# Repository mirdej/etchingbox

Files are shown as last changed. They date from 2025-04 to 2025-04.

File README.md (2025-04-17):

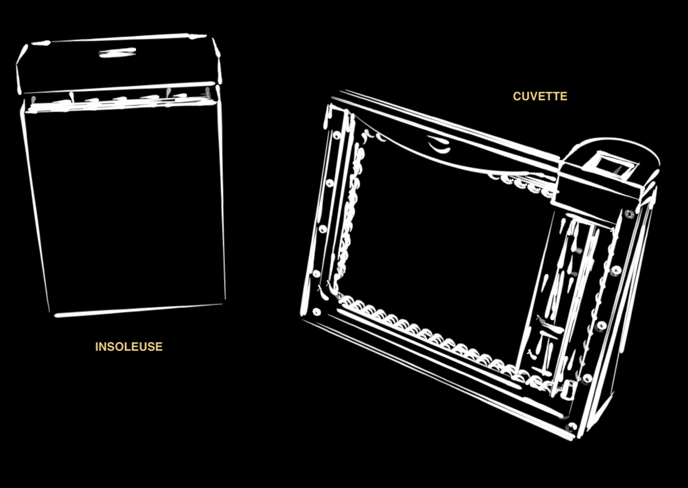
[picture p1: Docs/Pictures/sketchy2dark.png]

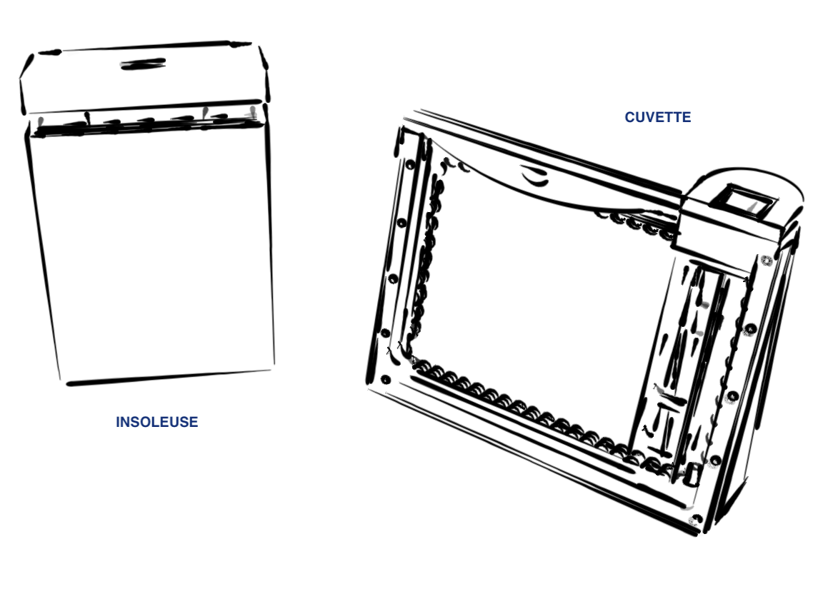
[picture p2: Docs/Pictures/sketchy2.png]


# AETZBOX
### DIY Mobile PCB Etching KIT

## The Idea 
Build a portable / mobile PCB etching workstation that fulfills these criteria
* waterproof
* able to etch 100x160mm double sided boards with 8mil precision
* low cost.  total bill of materials should not exceed 150 CHF
* diy approach, mostly laser cut plexi and easily sourceable materials
* fits in a RAKO Box

Some guiding ideas
* use very little but always fresh chemicals 
* good heat management: etching has to be done at 45-50 degrees celsius, developer has to be kept at >20 degrees as well (in my workshop, temperatures can easily drop below 16 degrees and developing is a pain).
* all material and chemicals travel in the box. liquid waste can travel in the box as well until it can properly disposed of.
* should be easy to clean. no electronics exposed to moisture. 
* as few as possible switches and electrical contacts exposed to the harsh etching environment
* self illuminating

## More Info
https://wiki.sgmk-ssam.ch/index.php/EtchingBox

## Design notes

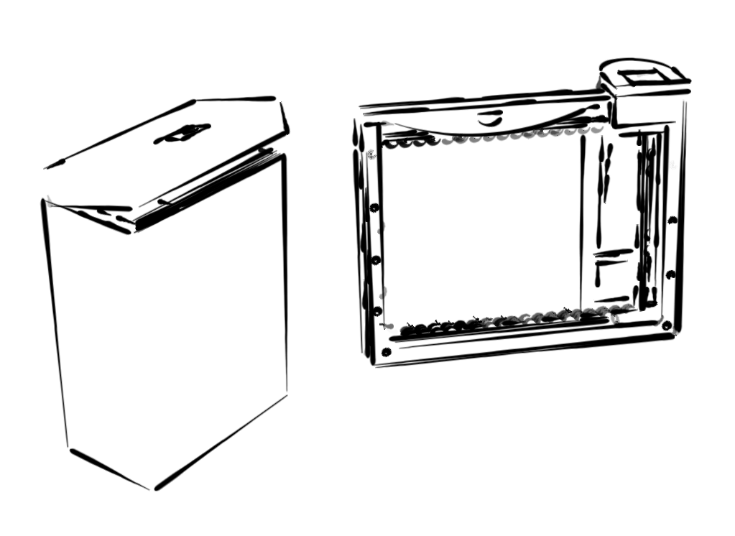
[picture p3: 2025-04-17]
Docs/Pictures/sketchy.png

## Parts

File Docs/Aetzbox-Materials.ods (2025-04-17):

Category | Description | Value | Qty | Price | Link
Total Cost |  |  |  | CHF 101.04
Chemicals
 | Developer | NaOH | 10g | CHF 0.13 | https://www.reichelt.com/ch/de/shop/produkt/entwickler_natriumhydroxid_1_kg-396207
 | Etchant | Natriumpersulfat | 600g | CHF 8.00 | https://www.reichelt.com/ch/de/shop/produkt/_etzmittel_natriumpersulfat_600_g_-23424
 | Presentisized PCB Material | Bungard 160x100mm one sided |  | CHF 2.15 | https://www.reichelt.com/ch/de/shop/produkt/fotoplatine_einseitig_160x100mm_1_5mm_35_-33767
 |  | Bungard 160x100mm double sided |  | CHF 2.70 | https://www.reichelt.com/ch/de/shop/produkt/fotoplatine_zweiseitig_160x100mm_1_5mm_35_-33774
Construction Material
 | PLA | Extrudr NX2 Black | About 850 grams, Total print time about 20 hours | CHF 25.50 | https://www.3dware.ch/en/search/93a7e009-72cb-4a7e-b261-3c64b5b91971?Query=01122210.25
 | Silicone | TFC Baseline 200 | About 300 grams | CHF 6.60 | https://trollfactory.de/Anwendungen/Modellbau/TFBL20010/TFC-Baseline-200-Silikon-Abformsilikon-Shore-35-1-1-transluzent-Groesse-10kg-5kg-5kg
 | Acrylic | 5mm clear, 5mm white opal, 3mm clear | About 50x50cm | CHF 25.00 | https://www.jumbo.ch/de/bauen-renovieren/bedachungsmaterialien/doppelstegplatten/acrylglas--50--50--05-cm/p/7009657
 | Screws | M4x40, Inox A2 | 14 | CHF 4.20 | https://www.bossard.com/eshop/ch-en/screws-and-bolts-with-internal-drive/hexalobular-6-lobe-socket-countersunk-flat-head-screws-fully-threaded/p/3803/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
 | Nuts | M4, Inox A2 | 14 | CHF 0.84 | https://www.bossard.com/eshop/ch-en/products/fastening-technology/standard-fastening-elements/nuts/hex-nuts/hex-nuts-08d/p/628/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
 | Screws | K22x6 |  | CHF 0.50 | https://www.bossard.com/eshop/ch-en/fastening-technology/direct-assembly-screws/direct-assembly-screws-for-plastics/ejot-pt/p/11308/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
Electronics
 | Temperature Sensor | Stainless Steel Waterproof DS18b20 | 1 | CHF 0.80 | https://www.aliexpress.com/item/32676135779.html
 | Aquarium Pump | TZT DC6-12V R385 Aquarium Fish Tank Round Water Air DC Diaphragm Pump | 1 | CHF 3.00 | https://www.aliexpress.com/item/1005003293750070.html
 | Heater | 304 Stainless Steel Cartridge Heater 8x80mm 60W 12V | 1 | CHF 2.00 | https://www.aliexpress.com/item/32906278667.html
 | Display | 0.96 inch oled IIC Serial White OLED Display Module 128X64 I2C SSD1315 12864 LCD | 2 | CHF 2.00 | https://www.aliexpress.com/item/4001028369082.html
 | ESP32 | ESP32-S3-WROOM | 2 | CHF 10.00 | https://www.digikey.ch/en/products/detail/espressif-systems/ESP32-S3-WROOM-1-N16/16162647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
 | PCBs | JLCPCB |  | CHF 5.00
 | DC-DC Converter | 919-R-78K3.3-0.5 | 2 | CHF 5.60 | https://eu.mouser.com/ProductDetail/RECOM-Power/R-78K3.3-0.5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
 | UV-Leds | S2-2835UVTA-0.2W |  |  | https://jlcpcb.com/partdetail/Tuozhan-S2_2835UVTA_02W/C2827317
 | Assembled UV-Board | JLCPCBA | 2 | CHF 10.00

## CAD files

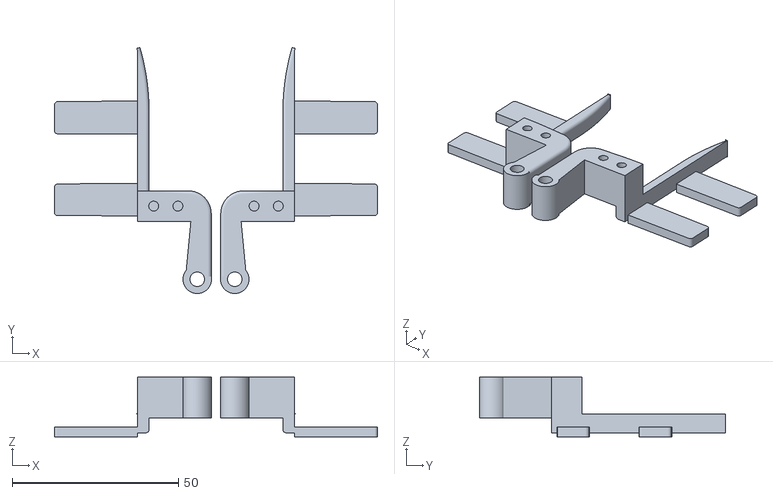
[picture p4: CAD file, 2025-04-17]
3D/STL/Insoleuse-Lid-Hinge.stl
97.3 x 74.1 x 18.0

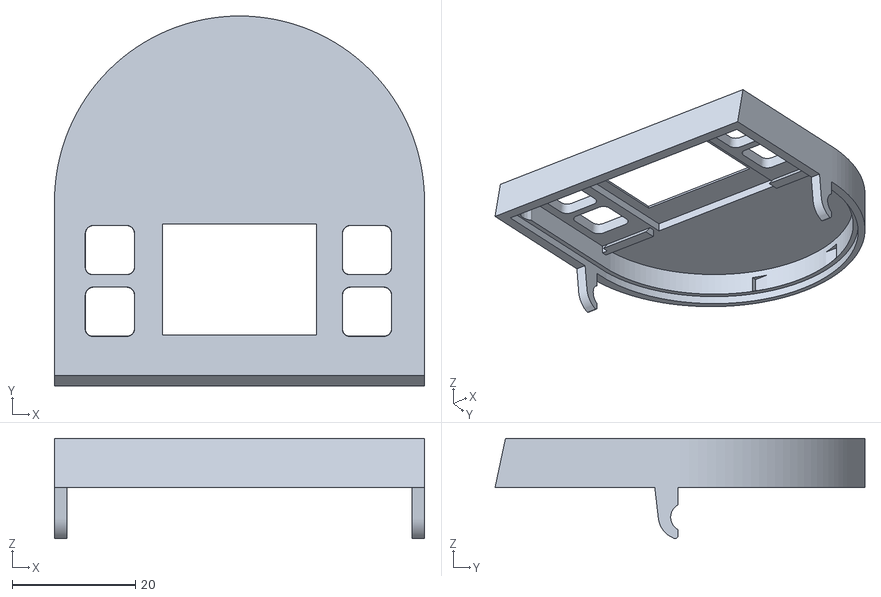
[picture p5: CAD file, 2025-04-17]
3D/STL/Cuvette-TopCover.stl
60.0 x 60.0 x 16.3

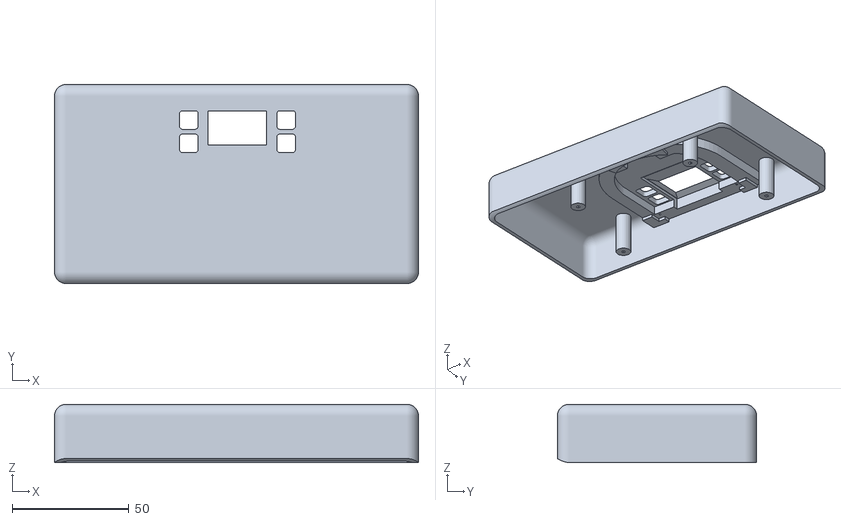
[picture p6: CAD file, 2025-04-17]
3D/STL/Insoleuse-Lid.stl
155.8 x 85.2 x 25.0

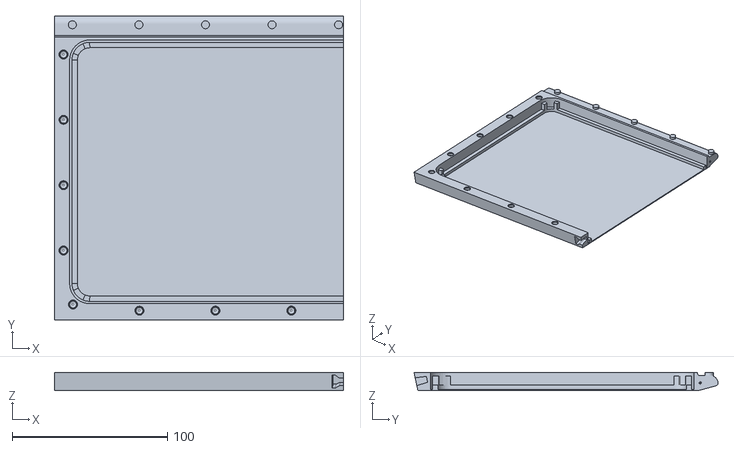
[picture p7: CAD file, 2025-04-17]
3D/STL/Cuvette-Back.stl
186.4 x 196.0 x 11.9

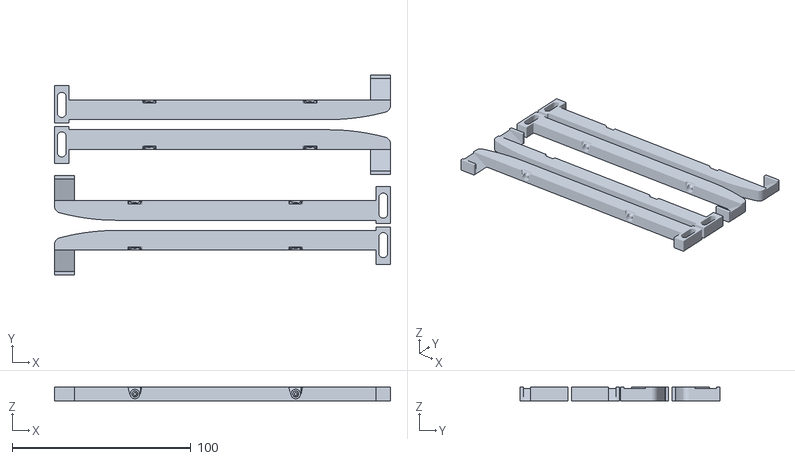
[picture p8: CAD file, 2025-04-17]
3D/STL/Insoleuse-Guides.stl
188.0 x 112.0 x 8.00

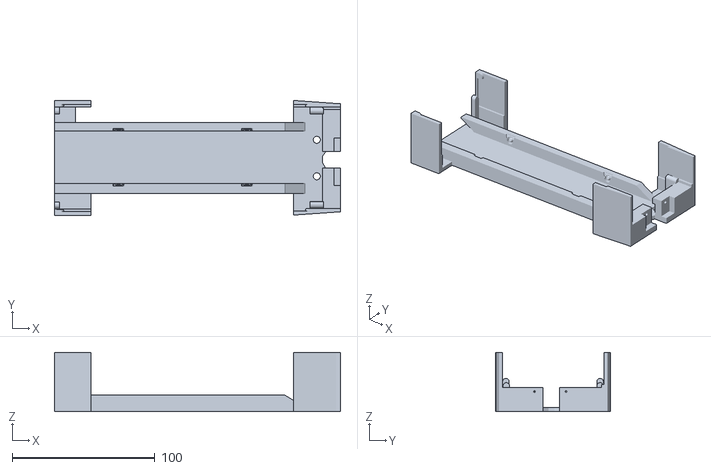
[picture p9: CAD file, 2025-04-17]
3D/STL/Insoleuse_GuideAndPCB-Holder.stl
200.6 x 80.9 x 41.6

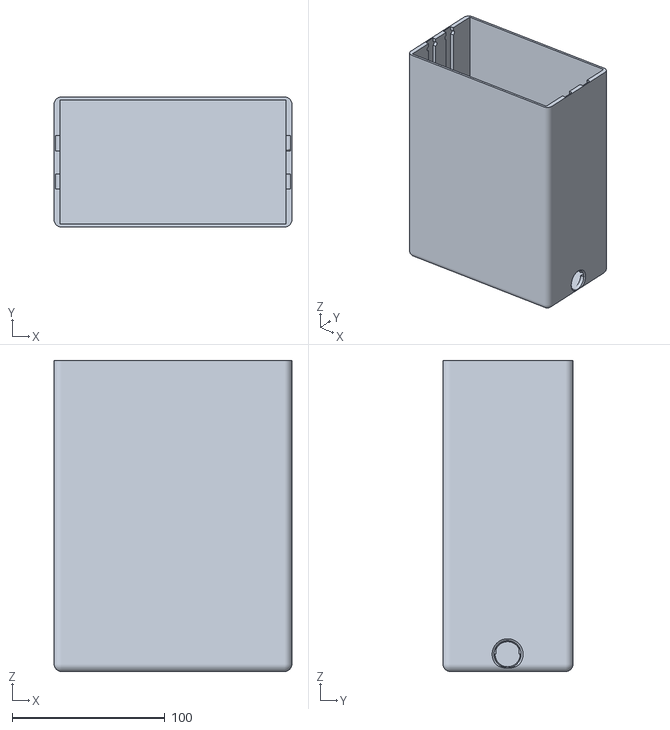
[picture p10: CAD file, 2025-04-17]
3D/STL/Insoleuse-Box.stl
155.8 x 85.2 x 203.6

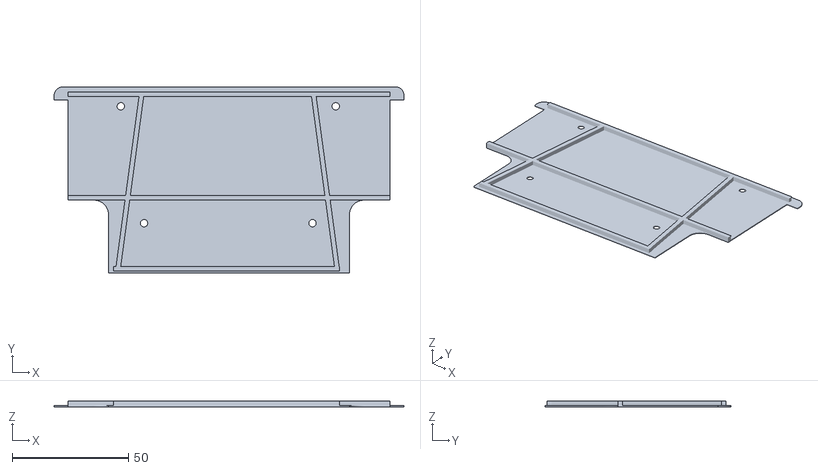
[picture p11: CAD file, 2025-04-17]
3D/STL/Insoleuse-Lid-Cover.stl
150.6 x 80.2 x 2.60

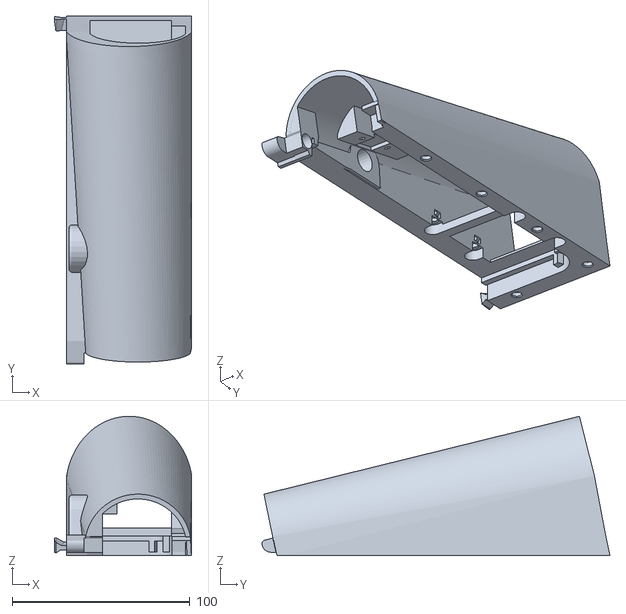
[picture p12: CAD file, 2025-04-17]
3D/STL/Cuvette-BackPumpCover.stl
77.4 x 196.0 x 78.5

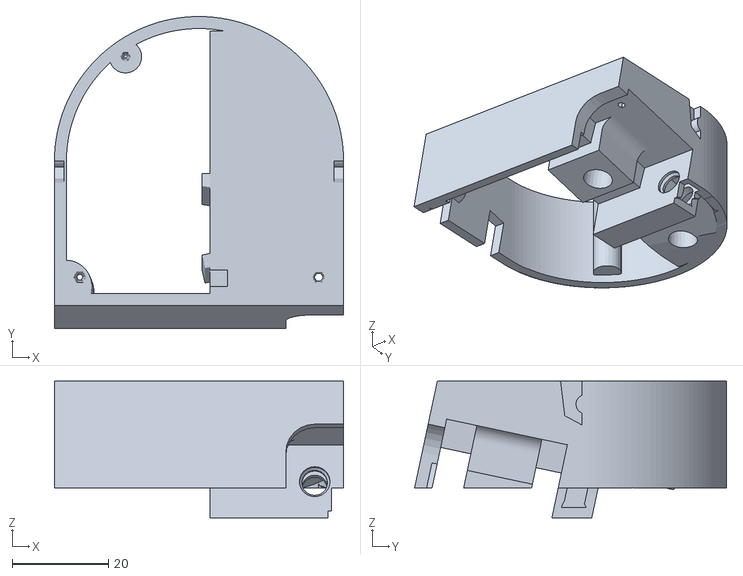
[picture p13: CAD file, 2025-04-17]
3D/STL/Cuvette-Top.stl
60.0 x 64.7 x 28.4

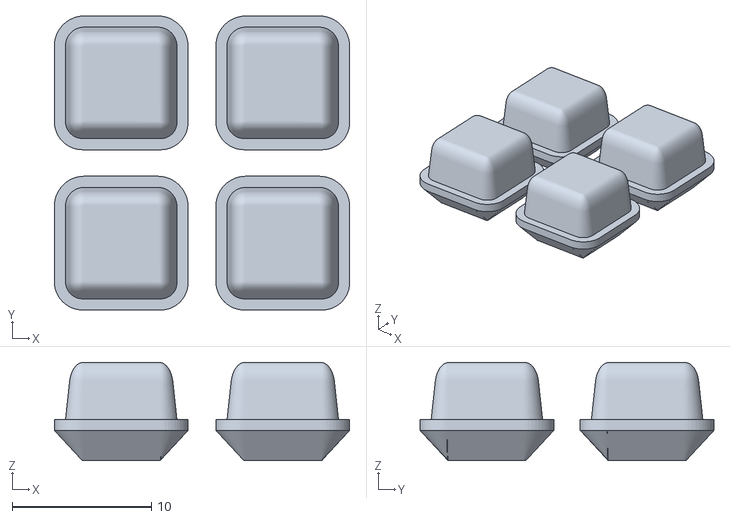
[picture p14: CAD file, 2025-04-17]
3D/STL/Insoleuse-Boutons.stl
21.2 x 21.1 x 7.04

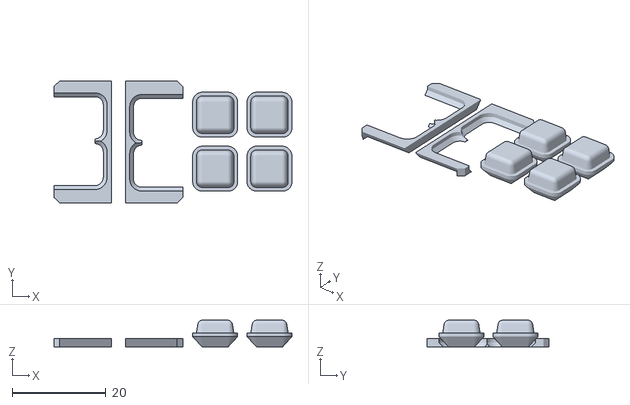
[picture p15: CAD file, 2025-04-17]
3D/STL/Cuvette-Boutons.stl
50.8 x 26.0 x 5.68

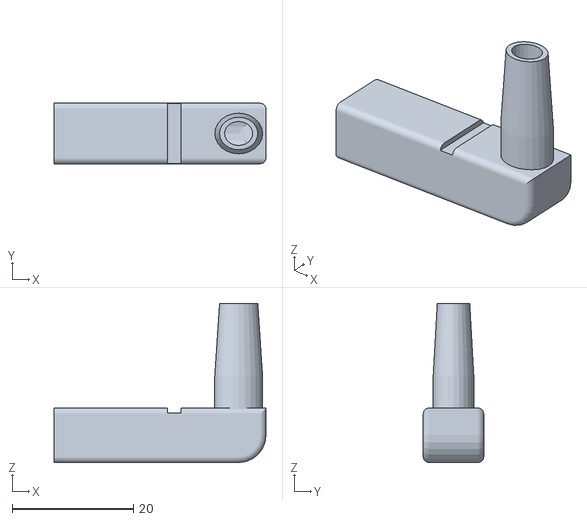
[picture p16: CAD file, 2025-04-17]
3D/STL/Cuvette-Blasfuss.stl
35.0 x 10.0 x 26.3

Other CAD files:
3D/Cuvette-Assembled.skp
3D/Cuvette-Mold-Bouchon.skp
3D/Cuvette-Mold-Cuvette.skp
3D/Cuvette-Mold-Lid.skp
3D/Cuvette-Mold-TopCover.skp
3D/Cuvette-Parts.skp
3D/Insoleuse-Assembled.skp
3D/Insoleuse-Parts.skp

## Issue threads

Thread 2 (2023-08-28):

heating chamber

5shekel, 2023-08-28:
hey, i love the etchingbox. had the pleasure of interacting with it at the cccamp.

i am missing a few things, mostly BOM of the heating chamber.
tips on the airflow/pump and heating element (ab)used will help.

https://github.com/mirdej/etchingbox/assets/222526/f30ac814-8d48-4f98-9d1f-8d26fef8e23c

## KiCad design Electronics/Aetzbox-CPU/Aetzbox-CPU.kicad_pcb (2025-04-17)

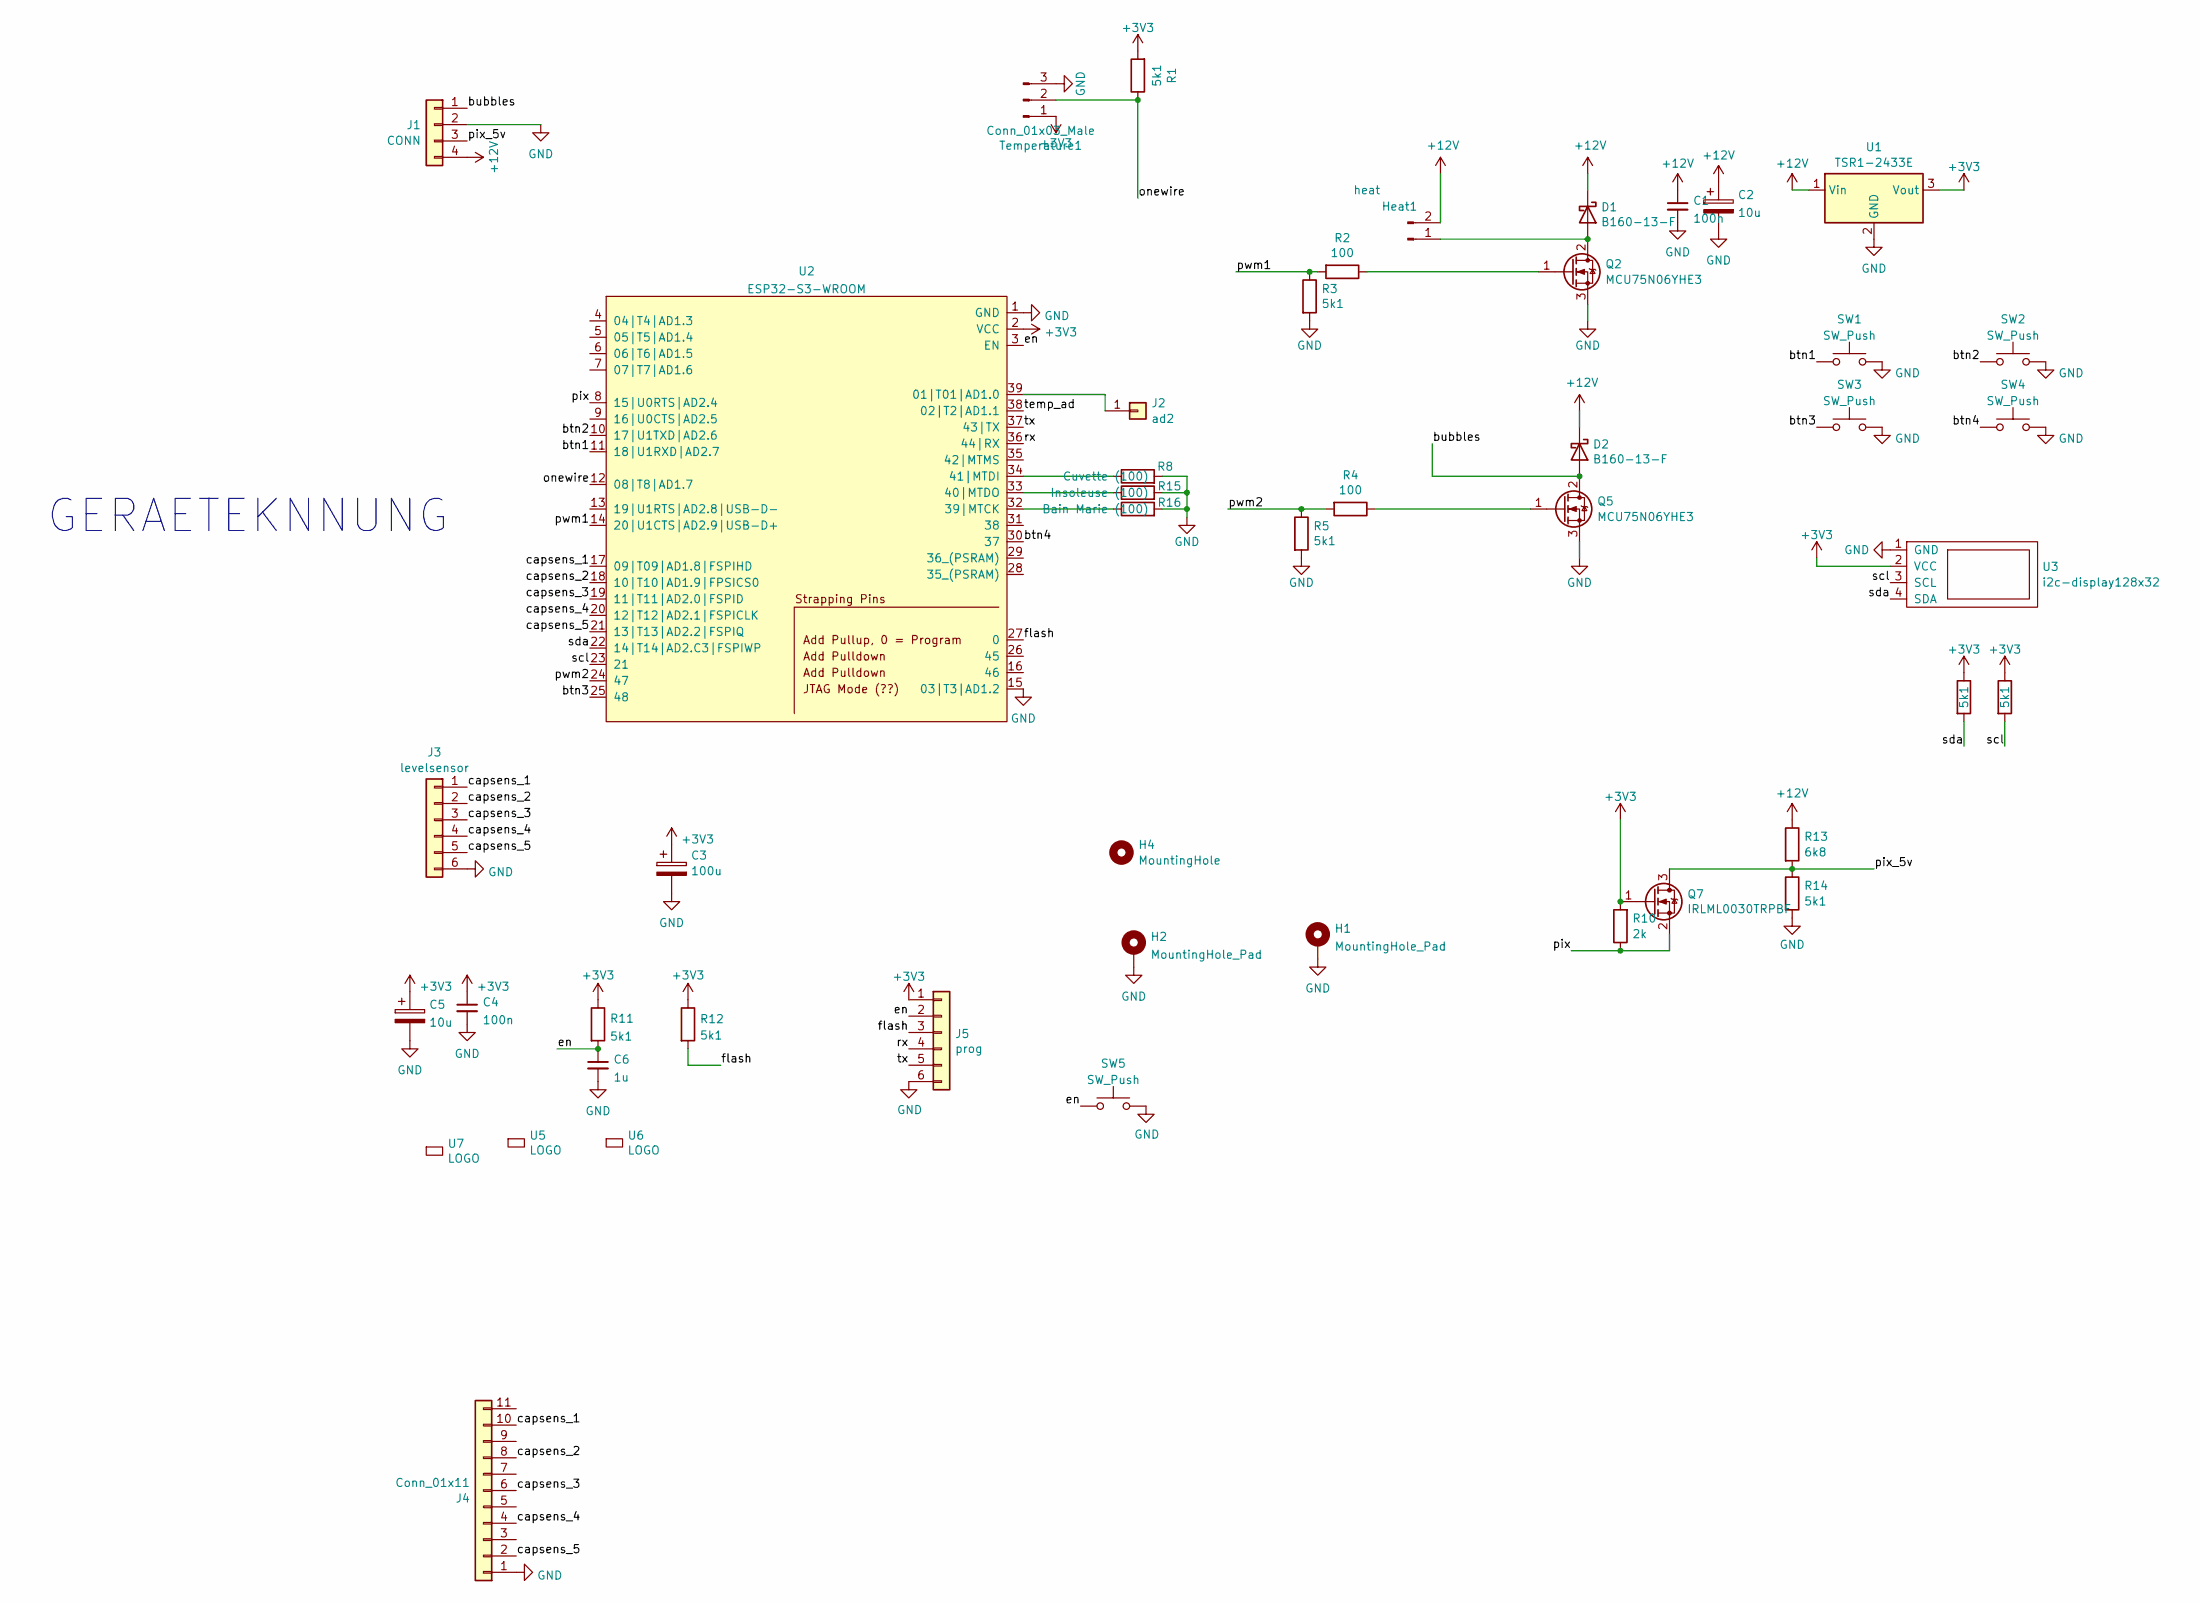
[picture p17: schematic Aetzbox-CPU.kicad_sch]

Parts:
C1, C4: 100n; C_0603_1608Metric_Pad1.05x0.95mm_HandSolder
C2, C5: 10u; C_1206_3216Metric_Pad1.42x1.75mm_HandSolder
C3: 100u; CP_EIA-6032-20_AVX-F
C6: 1u; C_0603_1608Metric_Pad1.05x0.95mm_HandSolder
D1, D2: B160-13-F; D_SMA-SMB_Universal_Handsoldering
H1, H2: MountingHole_Pad; MountingHole_2.5mm_Pad
H4: MountingHole; MountingHole_2.5mm
Heat1: heat; Molex_Mini-Fit_Jr_5566-02A_2x01_P4.20mm_Vertical
J1: CONN; Molex_Mini-Fit_Jr_5569-04A2_2x02_P4.20mm_H+V
J2: ad2; Solderpad_1mm
J3: levelsensor; PinSocket_1x06_P1.27mm_Vertical
J4: Conn_01x11; Molex_200528-0100_1x10-1MP_P1.00mm_Horizontal
J5: prog; ESP-POGO-PROG-THT
Q2, Q5: MCU75N06YHE3; TO-252-2
Q7: IRLML0030TRPBF; SOT-23
R1, R3, R5, R6, R7, R11, R12, R14: 5k1; R_0805_2012Metric
R2, R4: 100; R_0805_2012Metric
R8: Cuvette (100); R_0805_2012Metric
R10: 2k; R_0805_2012Metric
R13: 6k8; R_0805_2012Metric
R15: Insoleuse (100); R_0805_2012Metric
R16: Bain Marie (100); R_0805_2012Metric
SW1, SW2, SW3, SW4: SW_Push; Alps_Tactile_Switch
SW5: SW_Push; MiniButtonPLCC4
Temperature1: Conn_01x03_Male; Molex_KK-254_AE-6410-03A_1x03_P2.54mm_Vertical
U1: TSR1-2433E; Converter_DCDC_TRACO_TSR1-xxxxE_THT
U2: ESP32-S3-WROOM
U3: i2c-display128x32; Bangood_I2C_Display
U5: LOGO; logo_anyma_tiny
U6: LOGO; logo_sgmk
U7: LOGO; OSHW-Logo2_7.3x6mm_SilkScreen

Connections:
+3V3: C3.1, C4.1, C5.1, J5.1, Q7.1 (G), R1.2, R6.1, R7.1, R10.2, R11.1, R12.1, Temperature1.1, U1.3 (Vout), U2.2 (VCC), U3.2 (VCC)
+12V: C1.1, C2.1, D1.1 (K), D2.1 (K), Heat1.2, J1.4, R13.1, U1.1 (Vin)
/btn1: SW1.1, U2.11 (18|U1RXD|AD2.7)
/btn2: SW2.1, U2.10 (17|U1TXD|AD2.6)
/btn3: SW3.1, U2.25 (48)
/btn4: SW4.1, U2.30 (37)
/bubbles: D2.2 (A), J1.1, Q5.2 (D)
/capsens_1: J3.1, J4.10, U2.17 (09|T09|AD1.8|FSPIHD)
/capsens_2: J3.2, J4.8, U2.18 (10|T10|AD1.9|FPSICS0)
/capsens_3: J3.3, J4.6, U2.19 (11|T11|AD2.0|FSPID)
/capsens_4: J3.4, J4.4, U2.20 (12|T12|AD2.1|FSPICLK)
/capsens_5: J3.5, J4.2, U2.21 (13|T13|AD2.2|FSPIQ)
/en: C6.1, J5.2, R11.2, SW5.2, U2.3 (EN)
/flash: J5.3, R12.2, U2.27 (0)
/onewire: R1.1, Temperature1.2, U2.12 (08|T8|AD1.7)
/pix: Q7.2 (S), R10.1, U2.8 (15|U0RTS|AD2.4)
/pix_5v: J1.3, Q7.3 (D), R13.2, R14.1
/pwm1: R2.2, R3.1, U2.14 (20|U1CTS|AD2.9|USB-D+)
/pwm2: R4.2, R5.1, U2.24 (47)
/rx: J5.4, U2.36 (44|RX)
/scl: R7.2, U2.23 (21), U3.3 (SCL)
/sda: R6.2, U2.22 (14|T14|AD2.C3|FSPIWP), U3.4 (SDA)
/temp_ad: U2.38 (02|T2|AD1.1)
/tx: J5.5, U2.37 (43|TX)
GND: C1.2, C2.2, C3.2, C4.2, C5.2, C6.2, H1.1, H2.1, J1.2, J3.6, J4.1, J5.6, Q2.3 (S), Q5.3 (S), R3.2, R5.2, R8.2, R14.2, R15.2, R16.2, SW1.2, SW2.2, SW3.2, SW4.2, SW5.1, Temperature1.3, U1.2 (GND), U2.1 (GND), U2.15 (03|T3|AD1.2), U2.40 (GND), U2.41 (GND), U3.1 (GND)
unnamed: D1.2 (A), Heat1.1, Q2.2 (D)
unnamed: J2.1, U2.39 (01|T01|AD1.0)
unnamed: Q2.1 (G), R2.1
unnamed: Q5.1 (G), R4.1
unnamed: R16.1, U2.32 (39|MTCK)
unnamed: R15.1, U2.33 (40|MTDO)
unnamed: R8.1, U2.34 (41|MTDI)

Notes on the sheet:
GERAETEKNNUNG

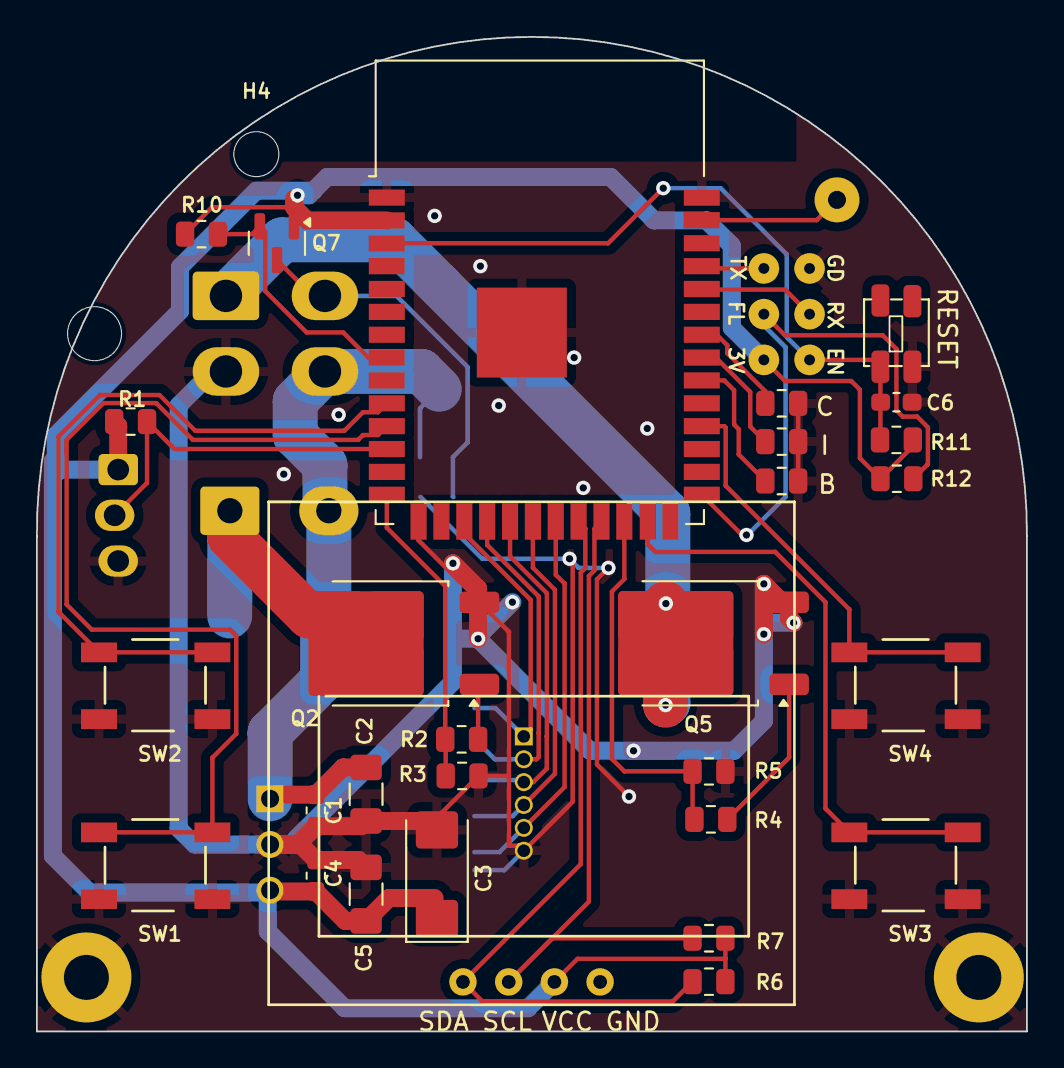
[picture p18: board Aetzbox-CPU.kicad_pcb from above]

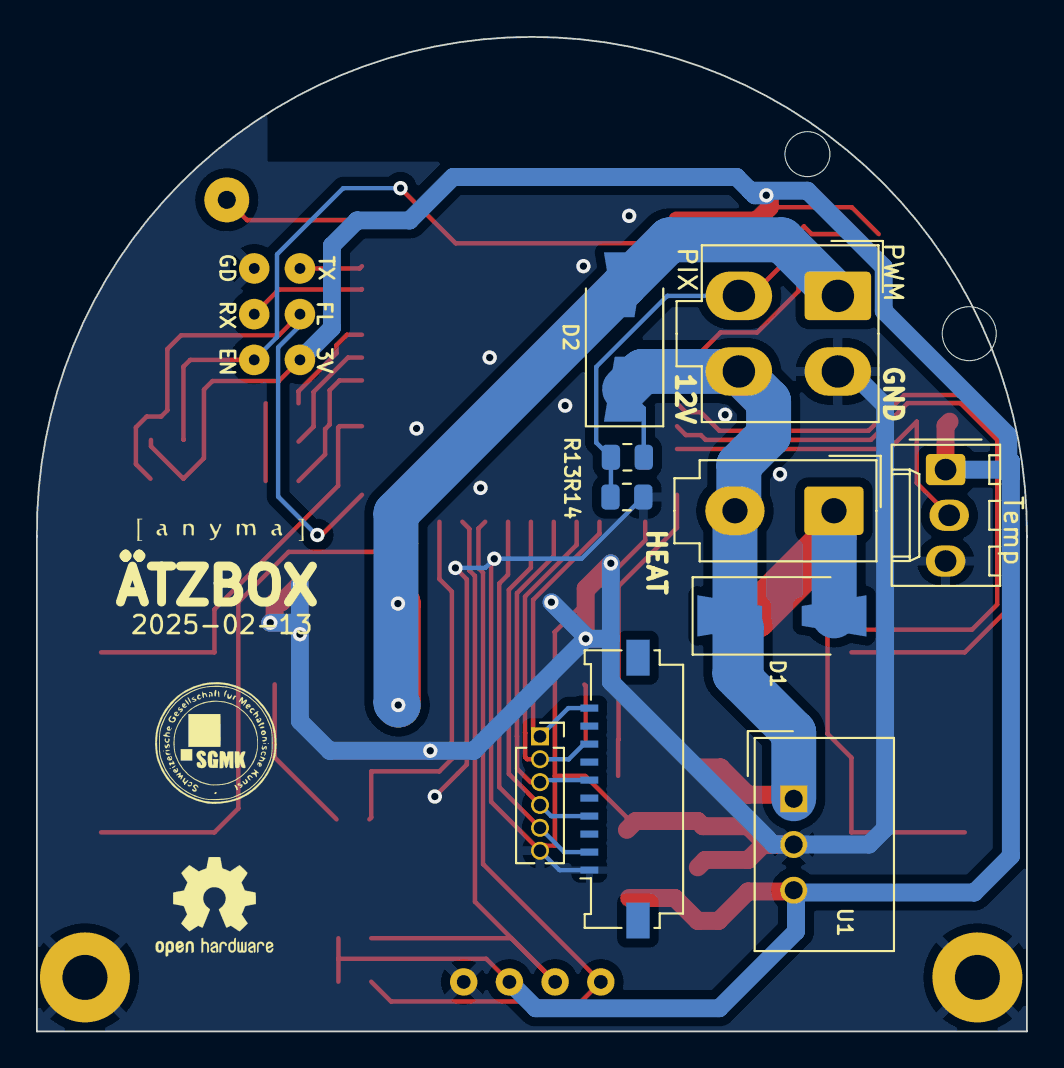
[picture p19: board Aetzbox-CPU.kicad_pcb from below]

Board: 2 copper layers, 55.0 x 55.3 mm, 47 parts (14 on the bottom side), 31 nets.

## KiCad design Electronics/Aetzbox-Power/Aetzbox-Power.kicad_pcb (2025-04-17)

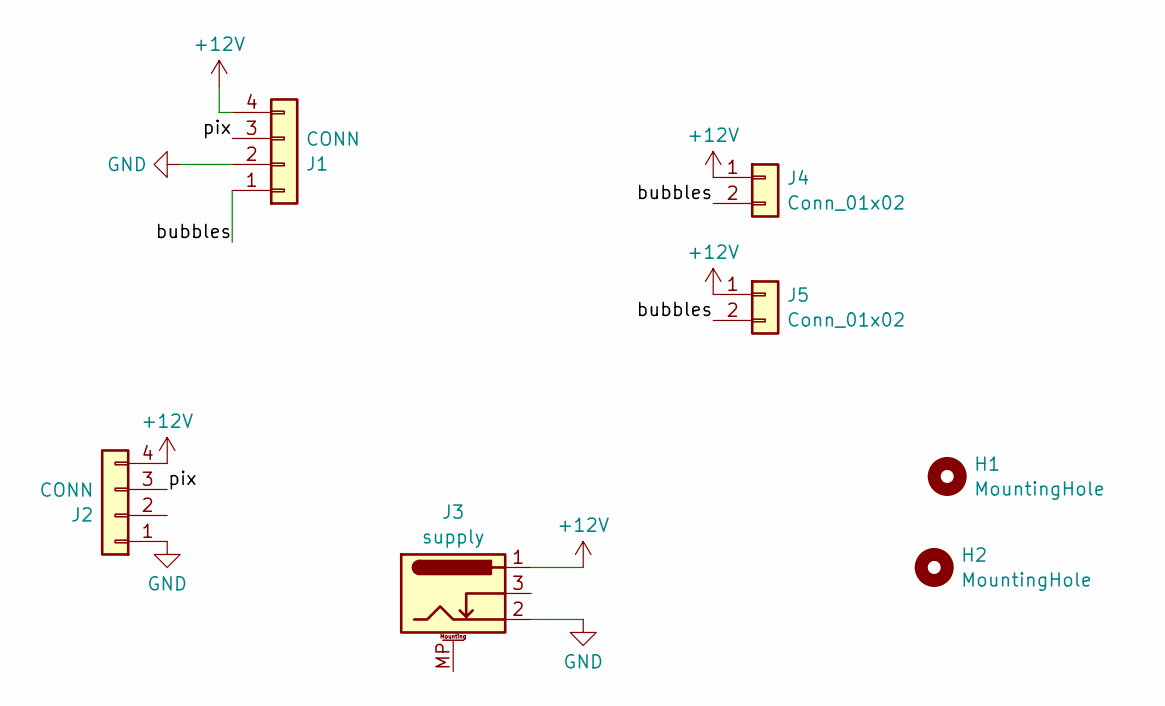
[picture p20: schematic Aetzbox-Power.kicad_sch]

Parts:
H1, H2: MountingHole; MountingHole_3.2mm_M3_DIN965
J1: CONN; Molex_Mini-Fit_Jr_5569-04A2_2x02_P4.20mm_H+V
J2: CONN; PinHeader_1x04_P2.54mm_Horizontal
J3: supply; BarrelJack_CUI_PJ-079BH_Horizontal
J4, J5: Conn_01x02; PinHeader_1x02_P2.54mm_Horizontal

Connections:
+12V: J1.4, J2.4, J3.1, J4.1, J5.1
/bubbles: J1.1, J4.2, J5.2
/pix: J1.3, J2.3
GND: J1.2, J2.1, J3.2

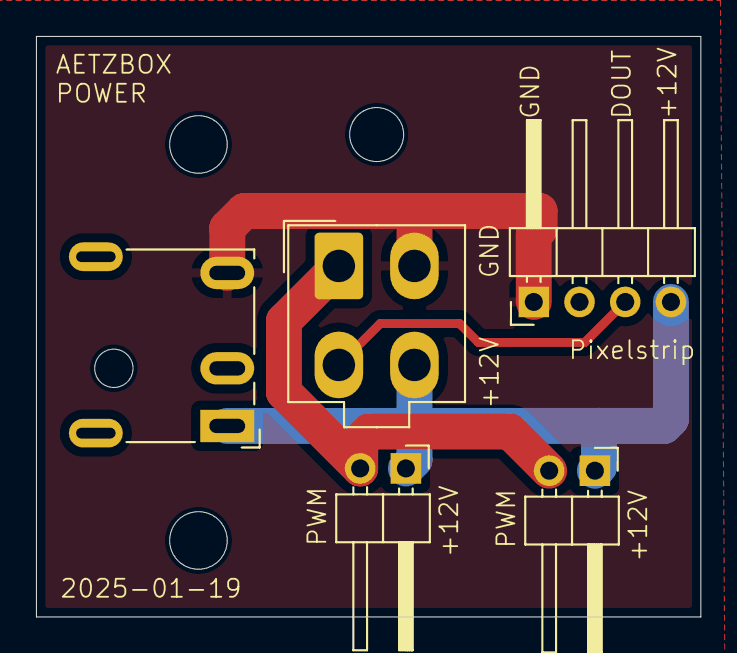
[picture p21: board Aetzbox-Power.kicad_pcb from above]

Board: 2 copper layers, 36.9 x 32.2 mm, 7 parts (0 on the bottom side), 4 nets.

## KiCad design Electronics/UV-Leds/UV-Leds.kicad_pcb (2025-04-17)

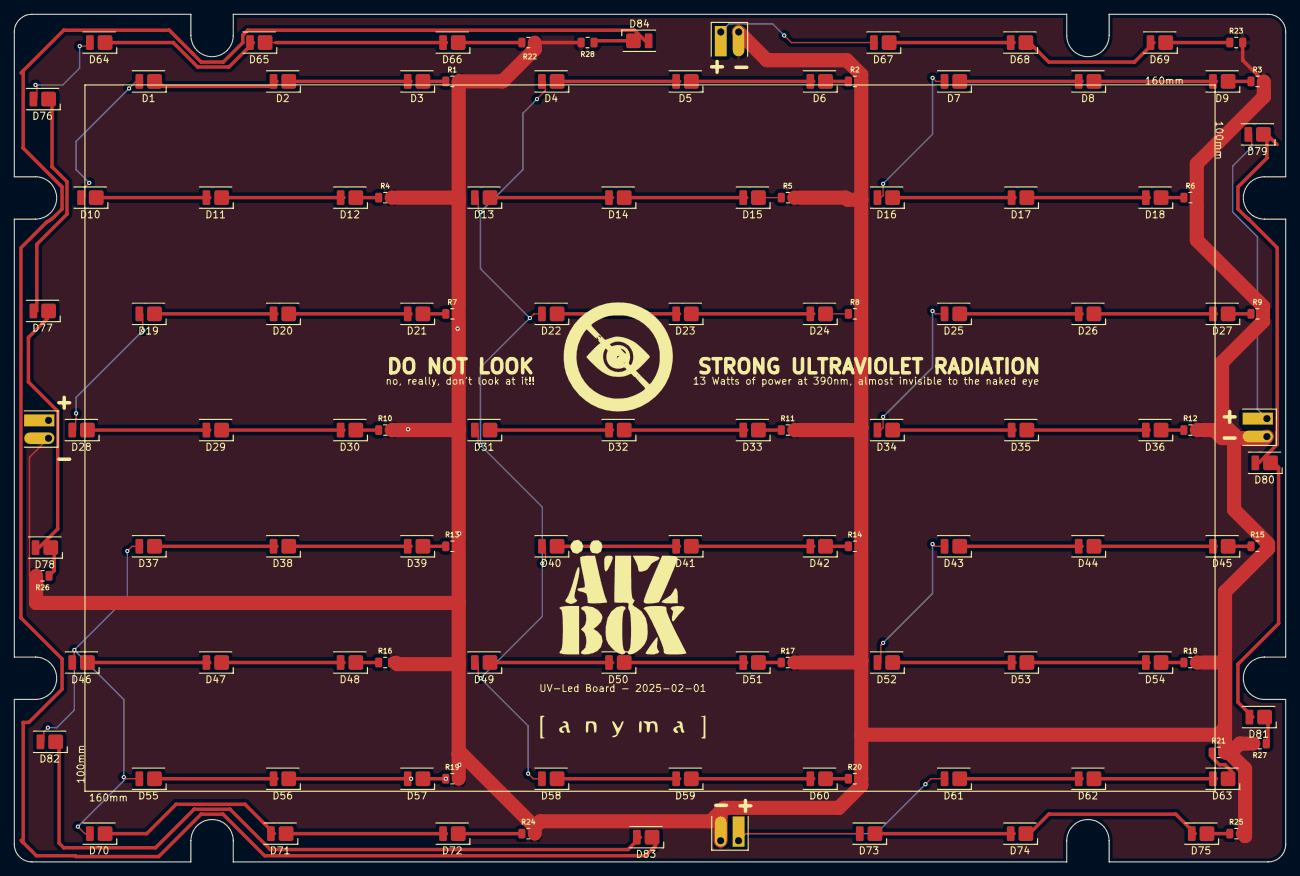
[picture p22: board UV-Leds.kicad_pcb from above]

Board: 2 copper layers, 180.0 x 120.0 mm, 119 parts (0 on the bottom side), 86 nets.

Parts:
D1, D2, D3, D4, D5, D6, D7, D8, D9, D10, D11, D12, D13, D14, D15, D16, D17, D18, D19, D20, D21, D22, D23, D24, D25, D26, D27, D28, D29, D30, D31, D32, D33, D34, D35, D36, D37, D38, D39, D40, D41, D42, D43, D44, D45, D46, D47, D48, D49, D50, D51, D52, D53, D54, D55, D56, D57, D58, D59, D60, D61, D62, D63, D64, D65, D66, D67, D68, D69, D70, D71, D72, D73, D74, D75, D76, D77, D78, D79, D80, D81, D82, D83, D84: LED; LED_2835_UV-S2-2835UVTA-0.2W
J1, J2, J3, J4: Conn_01x02; ComboPinhead_02
R1, R2, R3, R4, R5, R6, R7, R8, R9, R10, R11, R12, R13, R14, R15, R16, R17, R18, R19, R20, R21, R22, R23, R24, R25, R26, R27, R28: R; R_0805_2012Metric
U1: LOGO; logo_aetz_box
U2: LOGO; logo_dontt_look
U3: LOGO; logo_anyma

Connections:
+12V: D1.2 (A), D4.2 (A), D7.2 (A), D10.2 (A), D13.2 (A), D16.2 (A), D19.2 (A), D22.2 (A), D25.2 (A), D28.2 (A), D31.2 (A), D34.2 (A), D37.2 (A), D40.2 (A), D43.2 (A), D46.2 (A), D49.2 (A), D52.2 (A), D55.2 (A), D58.2 (A), D61.2 (A), D64.2 (A), D67.2 (A), D70.2 (A), D73.2 (A), D76.2 (A), D79.2 (A), D82.2 (A), J1.1, J2.1, J3.1, J4.1
GND: J1.2, J2.2, J3.2, J4.2, R1.2, R2.2, R3.2, R4.2, R5.2, R6.2, R7.2, R8.2, R9.2, R10.2, R11.2, R12.2, R13.2, R14.2, R15.2, R16.2, R17.2, R18.2, R19.2, R20.2, R21.2, R22.2, R23.2, R24.2, R25.2, R26.2, R27.2, R28.2
unnamed: D1.1 (K), D2.2 (A)
unnamed: D2.1 (K), D3.2 (A)
unnamed: D3.1 (K), R1.1
unnamed: D4.1 (K), D5.2 (A)
unnamed: D5.1 (K), D6.2 (A)
unnamed: D6.1 (K), R2.1
unnamed: D7.1 (K), D8.2 (A)
unnamed: D8.1 (K), D9.2 (A)
unnamed: D9.1 (K), R3.1
unnamed: D10.1 (K), D11.2 (A)
unnamed: D11.1 (K), D12.2 (A)
unnamed: D12.1 (K), R4.1
unnamed: D13.1 (K), D14.2 (A)
unnamed: D14.1 (K), D15.2 (A)
unnamed: D15.1 (K), R5.1
unnamed: D16.1 (K), D17.2 (A)
unnamed: D17.1 (K), D18.2 (A)
unnamed: D18.1 (K), R6.1
unnamed: D19.1 (K), D20.2 (A)
unnamed: D20.1 (K), D21.2 (A)
unnamed: D21.1 (K), R7.1
unnamed: D22.1 (K), D23.2 (A)
unnamed: D23.1 (K), D24.2 (A)
unnamed: D24.1 (K), R8.1
unnamed: D25.1 (K), D26.2 (A)
unnamed: D26.1 (K), D27.2 (A)
unnamed: D27.1 (K), R9.1
unnamed: D28.1 (K), D29.2 (A)
unnamed: D29.1 (K), D30.2 (A)
unnamed: D30.1 (K), R10.1
unnamed: D31.1 (K), D32.2 (A)
unnamed: D32.1 (K), D33.2 (A)
unnamed: D33.1 (K), R11.1
unnamed: D34.1 (K), D35.2 (A)
unnamed: D35.1 (K), D36.2 (A)
unnamed: D36.1 (K), R12.1
unnamed: D37.1 (K), D38.2 (A)
unnamed: D38.1 (K), D39.2 (A)
unnamed: D39.1 (K), R13.1
unnamed: D40.1 (K), D41.2 (A)
unnamed: D41.1 (K), D42.2 (A)
unnamed: D42.1 (K), R14.1
unnamed: D43.1 (K), D44.2 (A)
unnamed: D44.1 (K), D45.2 (A)
unnamed: D45.1 (K), R15.1
unnamed: D46.1 (K), D47.2 (A)
unnamed: D47.1 (K), D48.2 (A)
unnamed: D48.1 (K), R16.1
unnamed: D49.1 (K), D50.2 (A)
unnamed: D50.1 (K), D51.2 (A)
unnamed: D51.1 (K), R17.1
unnamed: D52.1 (K), D53.2 (A)
unnamed: D53.1 (K), D54.2 (A)
unnamed: D54.1 (K), R18.1
unnamed: D55.1 (K), D56.2 (A)
unnamed: D56.1 (K), D57.2 (A)
unnamed: D57.1 (K), R19.1
unnamed: D58.1 (K), D59.2 (A)
unnamed: D59.1 (K), D60.2 (A)
unnamed: D60.1 (K), R20.1
unnamed: D61.1 (K), D62.2 (A)
unnamed: D62.1 (K), D63.2 (A)
unnamed: D63.1 (K), R21.1
unnamed: D64.1 (K), D65.2 (A)
unnamed: D65.1 (K), D66.2 (A)
unnamed: D66.1 (K), R22.1
unnamed: D67.1 (K), D68.2 (A)
unnamed: D68.1 (K), D69.2 (A)
unnamed: D69.1 (K), R23.1
unnamed: D70.1 (K), D71.2 (A)
unnamed: D71.1 (K), D72.2 (A)
unnamed: D72.1 (K), R24.1
unnamed: D73.1 (K), D74.2 (A)
unnamed: D74.1 (K), D75.2 (A)
unnamed: D75.1 (K), R25.1
unnamed: D76.1 (K), D77.2 (A)
unnamed: D77.1 (K), D78.2 (A)
unnamed: D78.1 (K), R26.1
unnamed: D79.1 (K), D80.2 (A)
unnamed: D80.1 (K), D81.2 (A)
unnamed: D81.1 (K), R27.1
unnamed: D82.1 (K), D83.2 (A)
unnamed: D83.1 (K), D84.2 (A)
unnamed: D84.1 (K), R28.1

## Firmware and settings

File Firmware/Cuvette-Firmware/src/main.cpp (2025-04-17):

/*========================================================================================

[ a n y m a ]
AETZBOX
Cuvette

© 2024 Michael Egger AT anyma.ch

==========================================================================================*/
//                                                                                      LIB
#include <Arduino.h>
#include <FastLED.h>
#include <U8g2lib.h>
#include <OneWire.h>
#include <DallasTemperature.h>
#include "Logo.h"
#include <OTA.h>
#include <WiFiManager.h> // https://github.com/tzapu/WiFiManager



//----------------------------------------------------------------------------------------
//                                                                                  CONFIG
#define HW_VERSION 3
#define MAIN_FILE_SYSTEM LittleFS

#define LCDWidth u8g2.getDisplayWidth()
#define ALIGN_CENTER(t) ((LCDWidth - (u8g2.getUTF8Width(t))) / 2)
#define ALIGN_RIGHT(t) (LCDWidth - u8g2.getUTF8Width(t))
#define ALIGN_LEFT 0

#define NUM_CAPSENS 5
#define WATERLEVEL_CAP_THRESH 4

#if HW_VERSION == 2
#define NUM_BTNS 4
const int PIN_BTN[NUM_BTNS] = {18, 17, 47, 37};
const int PIN_CAP_SENS[NUM_CAPSENS] = {9, 10, 11, 12, 13};
#define PIN_SCL 21
#define PIN_SDA 14
#define PIN_TC1047 2
#define PIN_ONE_WIRE_BUS 20
#define PIN_PWM_HEAT 16
#define PIN_PWM_BUBBLES 38
#define PIN_PWM_AUX 48
#define PIN_PIX 15
#endif

#if HW_VERSION == 3
#define NUM_BTNS 4
const int PIN_BTN[NUM_BTNS] = {18, 17, 48, 37};
const int PIN_CAP_SENS[NUM_CAPSENS] = {9, 10, 11, 12, 13};
#define PIN_SCL 21
#define PIN_SDA 14
#define PIN_TC1047 -1
#define PIN_ONE_WIRE_BUS 8
#define PIN_PWM_HEAT 20
#define PIN_PWM_BUBBLES 47
#define PIN_PWM_AUX -1
#define PIN_PIX 15
#endif

#define LED_FREQ 5000
#define LED_RESOLUTION 8
#define LED_CHANN 0

#define BUBBLES_FREQ 50
#define BUBBLES_RESOLUTION 8
#define BUBBLES_CHANN 1

#define DISPLAY_MODE_IDLE 0
#define DISPLAY_MODE_INFO 1
#define DISPLAY_TIMEOUT 10000

#define NUM_PIXELS 48

#pragma message("Building with device name:" DEVICE_NAME)
//----------------------------------------------------------------------------------------
//                                                                                 GLOBALS

U8G2_SSD1306_128X64_NONAME_F_HW_I2C u8g2(U8G2_R2, U8X8_PIN_NONE, PIN_SCL, PIN_SDA);
OneWire oneWire(PIN_ONE_WIRE_BUS);
DallasTemperature sensors(&oneWire);
CRGB pixel[NUM_PIXELS];

char message[128] = {0};
int display_mode;

int sens[NUM_CAPSENS];
int water_level;

float bubbles_target = 1.;
float bubbles_pwm = 0.5;

float led_target = 1.;
float led_pwm = 0.5;

float temperature_water_target = 46.;
float temperature_ambient, temperature_water;

//----------------------------------------------------------------------------------------

float mapfloat(float x, float in_min, float in_max, float out_min, float out_max)
{
  return (x - in_min) * (out_max - out_min) / (in_max - in_min) + out_min;
}

void print_sensor_values()
{
  Telnet.printf("Waterlevel %d\n", water_level);
  Telnet.print("Water sensor values -  ");
  for (int i = 0; i < NUM_CAPSENS; i++)
  {
    Telnet.printf("%d - ", sens[i]);
  }
  Telnet.println();
}
//----------------------------------------------------------------------------------------

int get_water_level()
{
  int waterlevel = 0;
  for (int i = 0; i < NUM_CAPSENS; i++)
  {
    sens[i] = touchRead(PIN_CAP_SENS[i]);
  }

  int reference = sens[0];
  if (reference < 10000)
  {
    Telnet.println("Weird Capacitive reference");
    waterlevel = -1;
    return waterlevel;
  }

  if (sens[4] / reference > WATERLEVEL_CAP_THRESH)
  {
    waterlevel = 1;
    if (sens[3] / reference > WATERLEVEL_CAP_THRESH)
    {
      waterlevel = 2;
      if (sens[2] / reference > WATERLEVEL_CAP_THRESH)
      {
        waterlevel = 3;
        if (sens[1] / reference > WATERLEVEL_CAP_THRESH)
        {
          waterlevel = 4;
        }
      }
    }
  }
  return waterlevel;
}

//----------------------------------------------------------------------------------------
//																	Nice and warm Welcome
void intro()
{

  u8g2.clearBuffer();
  u8g2.drawBitmap(0, 24, 16, 16, bitmap_anyma);
  u8g2.sendBuffer();
  delay(500);
  u8g2.drawBitmap(32, 0, 8, 48, bitmap_box);
  u8g2.sendBuffer();
  delay(50);
  u8g2.clearBuffer();
  u8g2.drawBitmap(32, 0, 8, 48, bitmap_box);
  u8g2.setFont(u8g2_font_missingplanet_tf);
  u8g2.setCursor(46, 64);
  u8g2.sendBuffer();
  delay(400);
  u8g2.print("Mark II");

  u8g2.sendBuffer();
  for (int hue = 0; hue < 360; hue++)
  {
    fill_rainbow(pixel, NUM_PIXELS, hue, 7);
    delay(5);
    FastLED.show();
  }
}

//========================================================================================
//----------------------------------------------------------------------------------------
//																				                                           TASKS

void wifi_task(void *)
{

  Telnet.printf("Start WIFI Task on core %d", xPortGetCoreID());

  // Wifi Manager: Try to connect, create access point on failure
  WiFiManager wm;
  bool res;
  res = wm.autoConnect(DEVICE_NAME); // anonymous ap

  if (!res)
  {
    Telnet.println("Failed to connect");
    // ESP.restart();
  }
  else
  {
    // if you get here you have connected to the WiFi
    Telnet.println("connected...yeey :)");

    OTA::start(DEVICE_NAME);

    while (1)
    {
      OTA::handle();
      delay(200);
    }
  }
}

//----------------------------------------------------------------------------------------
//																				                                      Button Task
void button_task(void *)
{

  Telnet.printf("Start Button Task on core %d", xPortGetCoreID());

  int last_button_state[NUM_BTNS];
  int button_state;

  for (int i = 0; i < NUM_BTNS; i++)
  {
    pinMode(PIN_BTN[i], INPUT_PULLUP);
    last_button_state[i] = digitalRead(PIN_BTN[i]);
  }

  Telnet.println("Running Button task");

  while (1)
  {
    for (int i = 0; i < NUM_BTNS; i++)
    {
      button_state = digitalRead(PIN_BTN[i]);
      if (button_state != last_button_state[i])
      {
        last_button_state[i] = button_state;
        if (!button_state)
        {
          Telnet.printf("Button %d pressed\n", i);

          if (display_mode == DISPLAY_MODE_INFO)
          {
            display_mode = DISPLAY_MODE_IDLE;
          }
          else
          {
            display_mode = DISPLAY_MODE_INFO;
          }
        }
      }
    }
    vTaskDelay(pdMS_TO_TICKS(100));
  }
}

//----------------------------------------------------------------------------------------
//																				                                      DISPLAY

void display_normal()
{
  u8g2.setCursor(0, 26);
  u8g2.setDrawColor(1);

  if (strlen(message))
  {
    u8g2.setFont(u8g2_font_logisoso18_tf);
    u8g2.setCursor(ALIGN_CENTER("-ERROR-"), 32);

    u8g2.print("-ERROR-");
    u8g2.setFont(u8g2_font_missingplanet_tf);
    u8g2.setCursor(ALIGN_CENTER(message), 48);
    u8g2.print(message);
  }
  else
  {

    if (digitalRead(PIN_PWM_HEAT))
    {
      u8g2.drawBox(0, 0, 128, 64);
      u8g2.setDrawColor(0);
    }
    u8g2.setFont(u8g2_font_logisoso38_tf);
    sprintf(message, "%.1f", temperature_water);

    u8g2.setFont(u8g2_font_logisoso38_tf);
    u8g2.setCursor(ALIGN_CENTER(message), 54);
    u8g2.print(message);
    u8g2.setDrawColor(1);
  }
}
//----------------------------------------------------------------------------------------
void display_wifi()
{
  u8g2.setCursor(0, 18);
  u8g2.setDrawColor(1);
  u8g2.setFont(u8g2_font_missingplanet_tf);
  if (WiFi.status() == WL_CONNECTED)
  {
    u8g2.printf("%s\n", WiFi.SSID().c_str());
    u8g2.setCursor(0, 36);
    u8g2.printf("%s.local\n", DEVICE_NAME);
  }
  else
  {
    u8g2.print("Wifi Not Connected");
  }
  u8g2.setCursor(0, 48);

  u8g2.printf("%s\n", FIRMWARE_VERSION);
  
}

//----------------------------------------------------------------------------------------
void update_display(void * = NULL)
{
  static long last_display_normal;
  if (millis() - last_display_normal > DISPLAY_TIMEOUT)
  {
    display_mode = DISPLAY_MODE_IDLE;
  }

  u8g2.clearBuffer();
  if (display_mode == DISPLAY_MODE_IDLE)
  {
    display_normal();
    last_display_normal = millis();
  }
  else
  {
    display_wifi();
  }
  u8g2.sendBuffer();
}

//----------------------------------------------------------------------------------------
//																				                                      CUVETTE Task

void cuvette_task(void *)
{
  Telnet.printf("Start Cuvette Task on core %d", xPortGetCoreID());

  pinMode(PIN_PWM_HEAT, OUTPUT);
  pinMode(PIN_PWM_BUBBLES, OUTPUT);

  digitalWrite(PIN_PWM_HEAT, HIGH);
  digitalWrite(PIN_PWM_BUBBLES, HIGH);
  delay(200);
  digitalWrite(PIN_PWM_HEAT, LOW);
  digitalWrite(PIN_PWM_BUBBLES, LOW);

  while (1)
  {
    message[0] = 0;
    sensors.requestTemperatures();
    float tempC = sensors.getTempCByIndex(0);
    if (tempC != DEVICE_DISCONNECTED_C)
    {
      temperature_water = tempC;
      if (temperature_water < 5.)
      {
        sprintf(message, "Water Freezing?");
      }

      if (temperature_water > 65.)
      {
        sprintf(message, "Water Too Hot!");
      }
    }
    else
    {
      sprintf(message, "Temp Sens Error");
      Telnet.println("Error: Could not read temperature data");
    }

    // check water level
    water_level = get_water_level();
    if (water_level < 0)
    {
      sprintf(message, "Water Sens Error");
    }
    else if (water_level < 2)
    {
      sprintf(message, "Water Low");
    }
    else if (water_level > 3)
    {
      sprintf(message, "Water Too High");
    }

    if (strlen(message))
    {
      Telnet.printf("Err: %d, %s\n", strlen(message), message);
    }

    if (strlen(message))
    {
      digitalWrite(PIN_PWM_HEAT, LOW);
      digitalWrite(PIN_PWM_BUBBLES, LOW);
      fill_solid(pixel, NUM_PIXELS, CRGB::OrangeRed);
    }
    else
    {
      fill_solid(pixel, NUM_PIXELS, CRGB::FloralWhite);

      if (temperature_water < temperature_water_target)
      {
        digitalWrite(PIN_PWM_HEAT, HIGH);
      }
      else
      {
        digitalWrite(PIN_PWM_HEAT, LOW);
      }
    }

    update_display();
    FastLED.show();
    vTaskDelay(pdMS_TO_TICKS(500));
  }
}

//========================================================================================
//----------------------------------------------------------------------------------------
//																				                                           Setup

void setup()
{
  FastLED.addLeds<WS2813, PIN_PIX, RGB>(pixel, NUM_PIXELS);
  FastLED.setBrightness(255);
  fill_solid(pixel, NUM_PIXELS, CRGB::FloralWhite);
  FastLED.show();

  Serial.begin(115200);
  vTaskDelay(pdMS_TO_TICKS(1000));

  Telnet.println("________________________");
  Telnet.printf("RESET Reason: %d\n", esp_reset_reason());
  Telnet.println("Setup");
  fill_solid(pixel, NUM_PIXELS, CRGB::Black);
  FastLED.show();

  xTaskCreatePinnedToCore(wifi_task, "Wifi-Task", 8096, NULL, 0, NULL, ARDUINO_RUNNING_CORE ? 0 : 1);

  u8g2.begin();
  u8g2.setPowerSave(0);
  fill_solid(pixel, NUM_PIXELS, CRGB::FloralWhite);
  FastLED.show();
  intro();

  xTaskCreate(cuvette_task, "Cuvette-Task", 8096, NULL, 0, NULL);
  xTaskCreate(button_task, "Button-Task", 8096, NULL, 0, NULL);

  display_mode = DISPLAY_MODE_INFO;

  Telnet.println("Setup Done");
  Telnet.println("________________________");
}

//========================================================================================
//----------------------------------------------------------------------------------------
//																				Loop
void loop()
{
  print_sensor_values();
  delay(4000);
}

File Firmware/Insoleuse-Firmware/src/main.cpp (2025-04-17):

/*========================================================================================

[ a n y m a ]
AETZBOX
Insoleuse


© 2024 Michael Egger AT anyma.ch

==========================================================================================*/
//                                                                                      LIB
#include <Arduino.h>
#include <FastLED.h>
#include <U8g2lib.h>

#include "Logo.h"
#include <OTA.h>
#include <WiFiManager.h> // https://github.com/tzapu/WiFiManager

#include "Preferences.h"

//----------------------------------------------------------------------------------------
//                                                                                  CONFIG

#define HW_VERSION 3

#define LCDWidth u8g2.getDisplayWidth()
#define ALIGN_CENTER(t) ((LCDWidth - (u8g2.getUTF8Width(t))) / 2)
#define ALIGN_RIGHT(t) (LCDWidth - u8g2.getUTF8Width(t))
#define ALIGN_LEFT 0

#define MAIN_FILE_SYSTEM LittleFS
#define NUM_CAPSENS 5

#if HW_VERSION == 2
#define NUM_BTNS 4
const int PIN_BTN[NUM_BTNS] = {18, 17, 47, 37};
const int PIN_CAP_SENS[NUM_CAPSENS] = {9, 10, 11, 12, 13};
#define PIN_SCL 21
#define PIN_SDA 14
#define PIN_TC1047 2
#define PIN_ONE_WIRE_BUS 20
#define PIN_PWM_HEAT 16
#define PIN_PWM_BUBBLES 38
#define PIN_PWM_AUX 48
#define PIN_PIX 15
#endif

#if HW_VERSION == 3
#define NUM_BTNS 4
const int PIN_BTN[NUM_BTNS] = {17, 18, 48, 37};
const int PIN_CAP_SENS[NUM_CAPSENS] = {9, 10, 11, 12, 13};
#define PIN_SCL 21
#define PIN_SDA 14
#define PIN_TC1047 -1
#define PIN_ONE_WIRE_BUS 8
#define PIN_PWM_HEAT 20
#define PIN_UV_LEDS 47
#define PIN_PWM_AUX -1
#define PIN_PIX 15
#endif

#define NUM_PIXELS 1
#define BTN_MODIFY 0
#define BTN_CANCEL 1
#define BTN_DOWN 2
#define BTN_UP 3

enum State
{
  FRESH,
  RUN,
  DONE,
  MODIFY

};

int exposure_target_seconds = 120;
int exposure_seconds = 0;
long exposure_start_millis;
long exposure_stop_millis;
State state = FRESH;

#pragma message("Building with device name:" DEVICE_NAME)

//----------------------------------------------------------------------------------------
//                                                                                 GLOBALS

CRGB pixel[NUM_PIXELS];
U8G2_SSD1306_128X64_NONAME_F_HW_I2C u8g2(U8G2_R2, U8X8_PIN_NONE, PIN_SCL, PIN_SDA);
Preferences preferences;

//----------------------------------------------------------------------------------------

void startExposure()
{
  state = RUN;
  Telnet.println("Exposure start");

  exposure_start_millis = millis();
  digitalWrite(PIN_UV_LEDS, HIGH);
}

//----------------------------------------------------------------------------------------

void stopExposure()
{
  state = DONE;
  Telnet.println("Exposure done");
  exposure_stop_millis = millis();
  digitalWrite(PIN_UV_LEDS, LOW);
}

//----------------------------------------------------------------------------------------
//																	Nice and warm Welcome
void intro()
{

  u8g2.clearBuffer();
  u8g2.drawBitmap(0, 24, 16, 16, bitmap_anyma);
  u8g2.sendBuffer();
  delay(500);
  u8g2.drawBitmap(32, 0, 8, 48, bitmap_box);
  u8g2.sendBuffer();
  delay(50);
  u8g2.clearBuffer();
  u8g2.drawBitmap(32, 0, 8, 48, bitmap_box);
  u8g2.setFont(u8g2_font_missingplanet_tf);
  u8g2.setCursor(46, 64);
  u8g2.sendBuffer();
  delay(400);
  u8g2.print("Mark II");
  u8g2.sendBuffer();

  delay(600);
  u8g2.clearBuffer();
  u8g2.drawBitmap(32, 0, 8, 48, bitmap_box);
  u8g2.setFont(u8g2_font_missingplanet_tf);
  u8g2.setCursor(38, 64);
  u8g2.print("INSOLEUSE");
  u8g2.sendBuffer();
}

void display_status(int time)
{

  u8g2.clearBuffer();
  u8g2.setCursor(0, 12);
  //  u8g2.setFont(u8g2_font_amstrad_cpc_extended_8r);
  u8g2.setFont(u8g2_font_missingplanet_tf);

  u8g2.print("MODIFY");
  u8g2.setCursor(100, 12);
  u8g2.setCursor(0, 64);
  u8g2.print("CANCEL");
  //u8g2.setCursor(48, 64);
  //u8g2.setCursor(100, 64);
  //u8g2.print("OFF");

  u8g2.setFont(u8g2_font_logisoso38_tf);

  char buf[128];
  sprintf(buf, "%ds", time);
  u8g2.setCursor(ALIGN_CENTER(buf), 54);
  u8g2.print(buf);

  u8g2.sendBuffer();
}

//----------------------------------------------------------------------------------------

void displayWaiting()
{
  int lastrun = (exposure_stop_millis - exposure_start_millis) / 1000;
  u8g2.clearBuffer();
  u8g2.drawBitmap(32, 0, 8, 48, bitmap_box);
  u8g2.setFont(u8g2_font_missingplanet_tf);

  char buf[128];
  sprintf(buf, "Runtime %d s", lastrun);
  u8g2.setCursor(ALIGN_CENTER(buf), 64);

  u8g2.printf(buf);
  u8g2.sendBuffer();
}

//========================================================================================
//----------------------------------------------------------------------------------------
//																				                                           TASKS

void wifi_task(void *)
{

  Telnet.printf("Start WIFI Task on core %d", xPortGetCoreID());

  // Wifi Manager: Try to connect, create access point on failure
  WiFiManager wm;
  bool res;
  res = wm.autoConnect(DEVICE_NAME); // anonymous ap

  if (!res)
  {
    Telnet.println("Failed to connect");
    // ESP.restart();
  }
  else
  {
    // if you get here you have connected to the WiFi
    Telnet.println("connected...yeey :)");

    OTA::start(DEVICE_NAME);

    while (1)
    {
      OTA::handle();
      delay(200);
    }
  }
}
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

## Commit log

2014-05-13 added first version of controler pcb and firmware
    [etch-control.brd, etch-control.sch]
2014-05-13 basic heater control
2018-11-13 make place for completely new version
    [etch-control.brd, etch-control.sch]
2018-11-16 new approach
    [Etchingbox_Controller.kicad_pcb, Etchingbox_Controller.sch]
2018-11-16 change mosfets, smaller borad
    [Etchingbox_Controller.kicad_pcb, Etchingbox_Controller.sch]
2018-11-26 Basic fuctions
    [Etchingbox_Controller.kicad_pcb, Etchingbox_Controller.sch]
2018-11-26 add sketchup models
    [Aetzbox.skp, Aetzbox~.skp, Bubbleunit.skp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]
2018-11-29 new bubble unit, holes for china plugs
    [Aetzbox.skp, Aetzbox~.skp, Bubbleunit.skp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]
2018-11-30 new basin holder
    [Aetzbox.skp, Aetzbox~.skp]
2018-11-30 4mm smaller lightpad.
    [Aetzbox.skp, Aetzbox~.skp]
2018-11-30 correct uv height. lighter lid, text
    [Aetzbox.skp, Aetzbox~.skp]
2018-11-30 some corrections
    [Aetzbox.skp, Aetzbox~.skp]
2018-12-01 fix missing link
    [Aetzbox.skp, Aetzbox~.skp]
2018-12-02 small corrections to holes. logo
    [Aetzbox.skp, Aetzbox~.skp, Tiefziehen.skp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]
2018-12-04 some minor hardware corrections during workshop. seperate logos. merge display code by dusjagr. add ambient temperatur display
    [Aetzbox.skp, Aetzbox~.skp, Bubbleunit.skp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]
2018-12-04 add lid holder
    [Deckelhalter.skp]
2019-02-08 add more sounds, temperature log option, safety check
    [Aetzbox.skp, Aetzbox~.skp, Bubbleunit.skp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]
2019-02-08 Using SAMD Timer 4 as slow PWM (crude way) to prevent whining of air pump
2019-02-11 prevent slow heat rate error when bath is warm)
2019-02-16 add new version of ub leds that should cover whole board
    [UV-Leds.kicad_pcb]
2021-07-26 stash latest version with MKR-Wifi before changing to ESP32
    [Etchingbox_Controller.sch]
2021-07-26 esp3 version
    [Etchingbox_Controller.kicad_pcb]
2022-04-10 add esp32 firmware
2025-04-17 2025 version hardware
    [Aetzbox-CPU.kicad_pcb, Aetzbox-CPU.kicad_sch, Aetzbox-Power.kicad_pcb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]
2025-04-17 rm hardware 2018
    [Etchingbox_Controller.kicad_pcb, Etchingbox_Controller.sch, UV-Leds.kicad_pcb]
2025-04-17 corret resistor value
    [UV-Leds.kicad_sch]
2025-04-17 add bom for uv led boards
2025-04-17 add bom
    [Aetzbox-Materials.ods]
2025-04-17 Add sketch
    [Aetzbox-Materials.ods]
2025-05-17 disable waterlevel sensor !!!
